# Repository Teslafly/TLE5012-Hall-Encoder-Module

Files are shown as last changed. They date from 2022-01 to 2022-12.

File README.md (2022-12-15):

# TLE5012-Hall-Encoder-Module
Breakout/mounting board for the TLE5012 hall encoder to use with the vesc motor controller project.

(Pictures are from my nearly identical as5047 encoder board at https://github.com/Teslafly/AS5047-Hall-Encoder-Module)

encoder boards with both connector orentations
top and bottom
example cables
kitting hardware
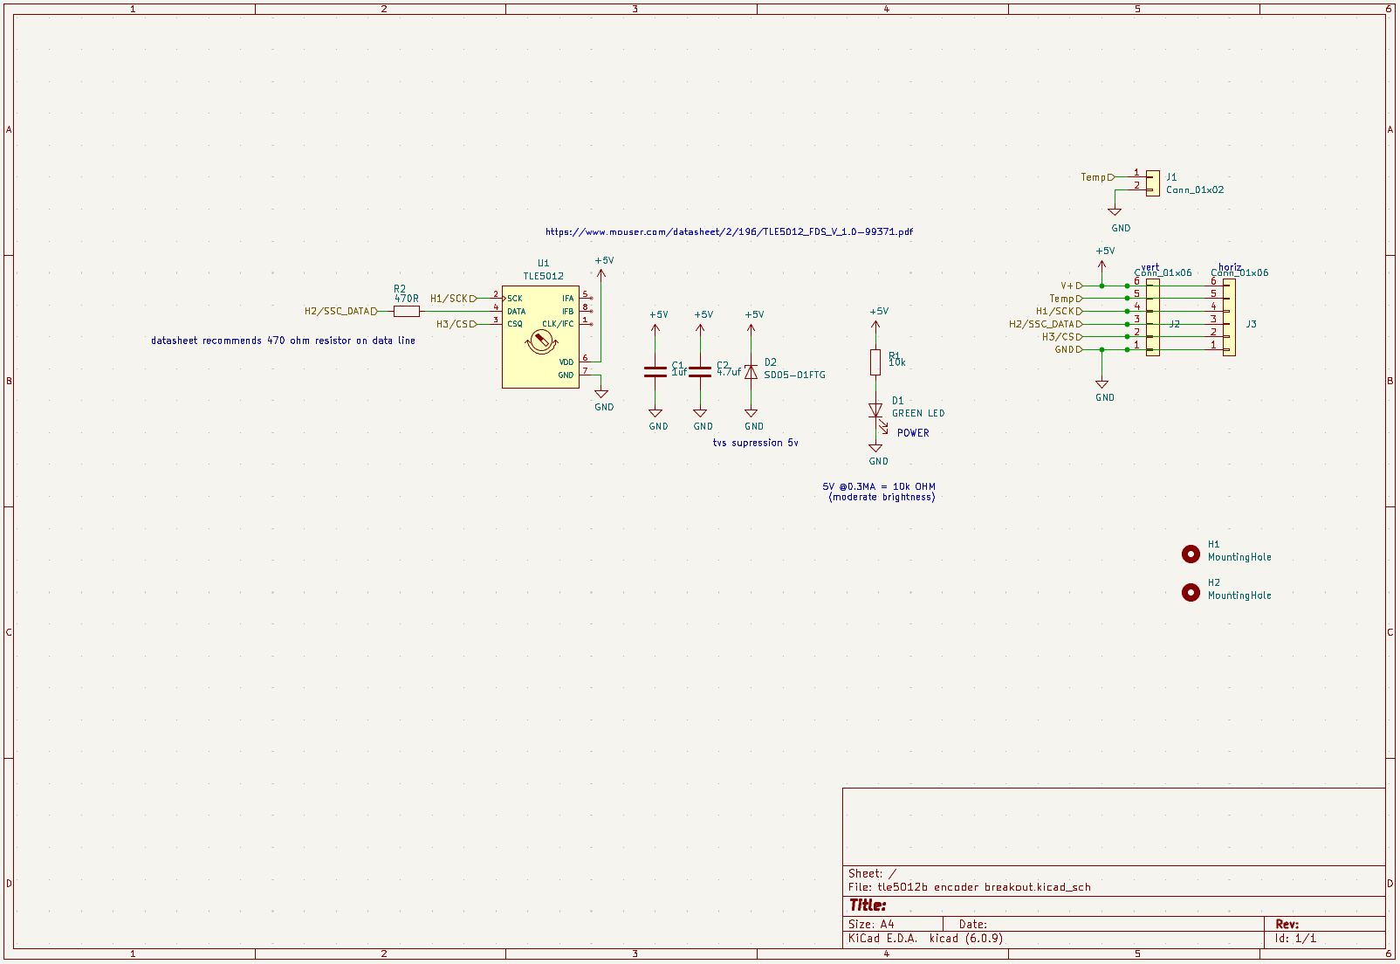
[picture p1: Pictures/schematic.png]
schematic


# Mounting:
- The mounting holes fit an m3 screw and are 16mm apart center to center.
- If the pcb cannot recess into the motor, a 3d printed shim (file link) can raise the encoder and provide clearance. If the motor gets too hot, the shim may be laser cut or milled out of a more resistant material.
- This encoder works with a diametric magnet fixed to the motor shaft. 
    - The magnet must be centered on the shaft. The encoder must be centered over the center of the magnet.
    - I find good results with a 6x2mm or 6x3mm neodymium magnet placed 1-5mm away from the face of the encoder.
    - Magnet example: https://www.aliexpress.us/item/3256801356246959.html

# Building:
- This pcb can be hand soldered easially.
- You can use either horizontal or vertical jst gh connectors for each connector placement. The vertical data connector should be placed with pins outwards to maintain the same pinout between the horizontal/vertical data connector options.
- As the temperature sensor connector is unpolarised, either horizontal or vertical connector can be placed on the same footprint. see pictures.

# JST GH mating connectors and making cables:
- If you do not have a crimper for JST GH crimps, they are fiddley and are hard to crimp properly.
I recommend either getting a male to male JST GH cable and cutting it to splice into a longer encoder cable, or doing the same with a precrimped silicone wire kit like this:
  - https://www.amazon.com/Pre-Crimped-Connectors-Pixhawk2-Pixracer-Silicone/dp/B07PBHN7TM/
  - Silicone wire is preferred due to it's durability and heat resistance. If you use pvc wire you should reinforce around the male GH connector with silocone rtv.

- The jst gh data connector has the same pinout as the JST PH vesc hall sensor connector.
however, note that some vesc hardwares that have swapped to JST GH connectors have reversed pinouts.
aka the cable must connect pins 1<->6, 2<->5, etc so that the locking clips are reversed from each other.
  - THIS IS NOT THE CASE ON ALL HARDWARES. CHECK YOUR PINOUT BEFORE POWERING.
    A REVERSED PINOUT WILL DESTROY THE ENCODER AS 5V AND GND ARE SWAPPED.
  - (The sensor should get lukewarm during operation. If it gets really hot then it's dead or a wire is shorted)

- Also, your vesc hardware must not have filters placed on the hall port pins. 
these filters must be removed for this encoder to work if present. They are present on all vesc hw 4.2, and nearly all flipsky boards. Trampa hw 6.0+ do not have these filters and will work as is.

### Wire:
I recommend using sheilded wire. usb cable will work in a pinch if you omot the temp wire and use the sheild for gnd. but ~28awg 6 core sheilded cable is ideal. the sheild should be connected to the gnd pin on the vesc side, and unconnected on the sensor side. you must keep all wires close to each other to get good signal integrity when splicing /crimping the end connectors.
If you cannot source sheilded wire, you will get acceptable results by keeping the wires close, and routing the cable away from the phase wires of the motor.
It is recommended that the data cable is kept under 0.5 meters. If that is not possible then sheilded wire must be used and attention to detail excercised in cable construction.

# Testing:
- This sensor runs best at 5V input power. 3.3V operation is not gaurenteed but will not cause damage.
- The led on the pcb should glow somewhat dimly. It is not blindingly bright.
- The sensor IC should get lukewarm during operation. If it gets really hot then it's dead or a wire is shorted

- You can troubleshoot/test the signal integrity of your cable and encoder functionality with the "`encoder`" command in the vesc terminal. 
  - The error rate should be very close to zero.
  - If it is above 0.5% then you should troubleshoot your setup and improve signal integrity. 
  - 99+% generally means that all communication with the encoder has failed. The wiring may be wrong, the sensor dead, or your vesc has hall port filters that need to be removed and shorted.
- when viewing the encoder angle in the vest-tool realtime view, the encoder value should change smoothly through the entire 360 degrees. If it is jumpy you probably have a signal integrity issue
- If the sensor cable is poorly routed/sheilded, high motor currents can cause noise that increases the encoder error rate. If you experience encoder faults during acceleration, check for intermittent opens in all signals and try rerouting the sensor cable away from motor phase wires and battery cables.
- a 3d printable test jig using a 608 bearing and 6mm magnet is included in the "`608 bearing test holder`" folder.

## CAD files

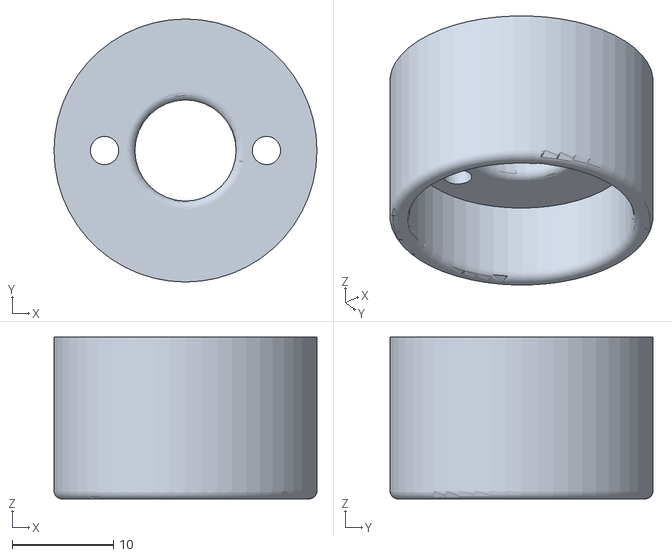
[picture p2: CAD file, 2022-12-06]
608 bearing test holder/bearing base-PartBody.stl
26.0 x 26.0 x 16.0

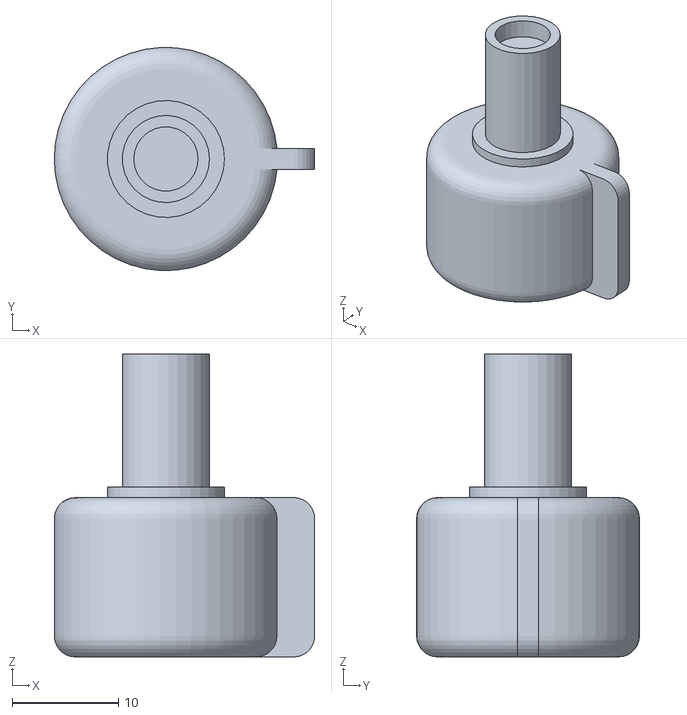
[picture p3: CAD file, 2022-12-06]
608 bearing test holder/knob-Body.stl
24.5 x 21.0 x 28.5

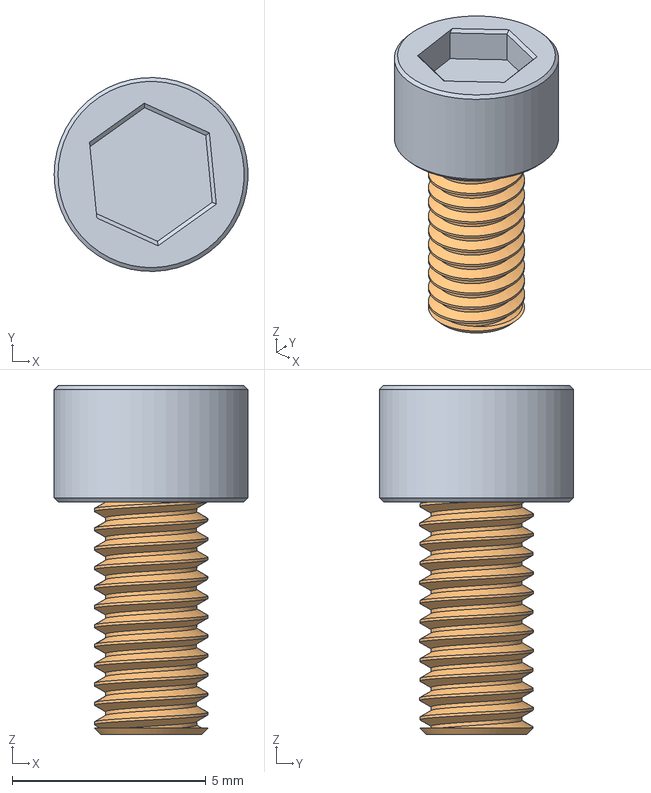
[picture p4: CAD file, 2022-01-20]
3d models/screw M3 6mm .step
5.00 x 5.00 x 9.00 mm

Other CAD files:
608 bearing test holder/knob.FCStd
608 bearing test holder/bearing base.FCStd

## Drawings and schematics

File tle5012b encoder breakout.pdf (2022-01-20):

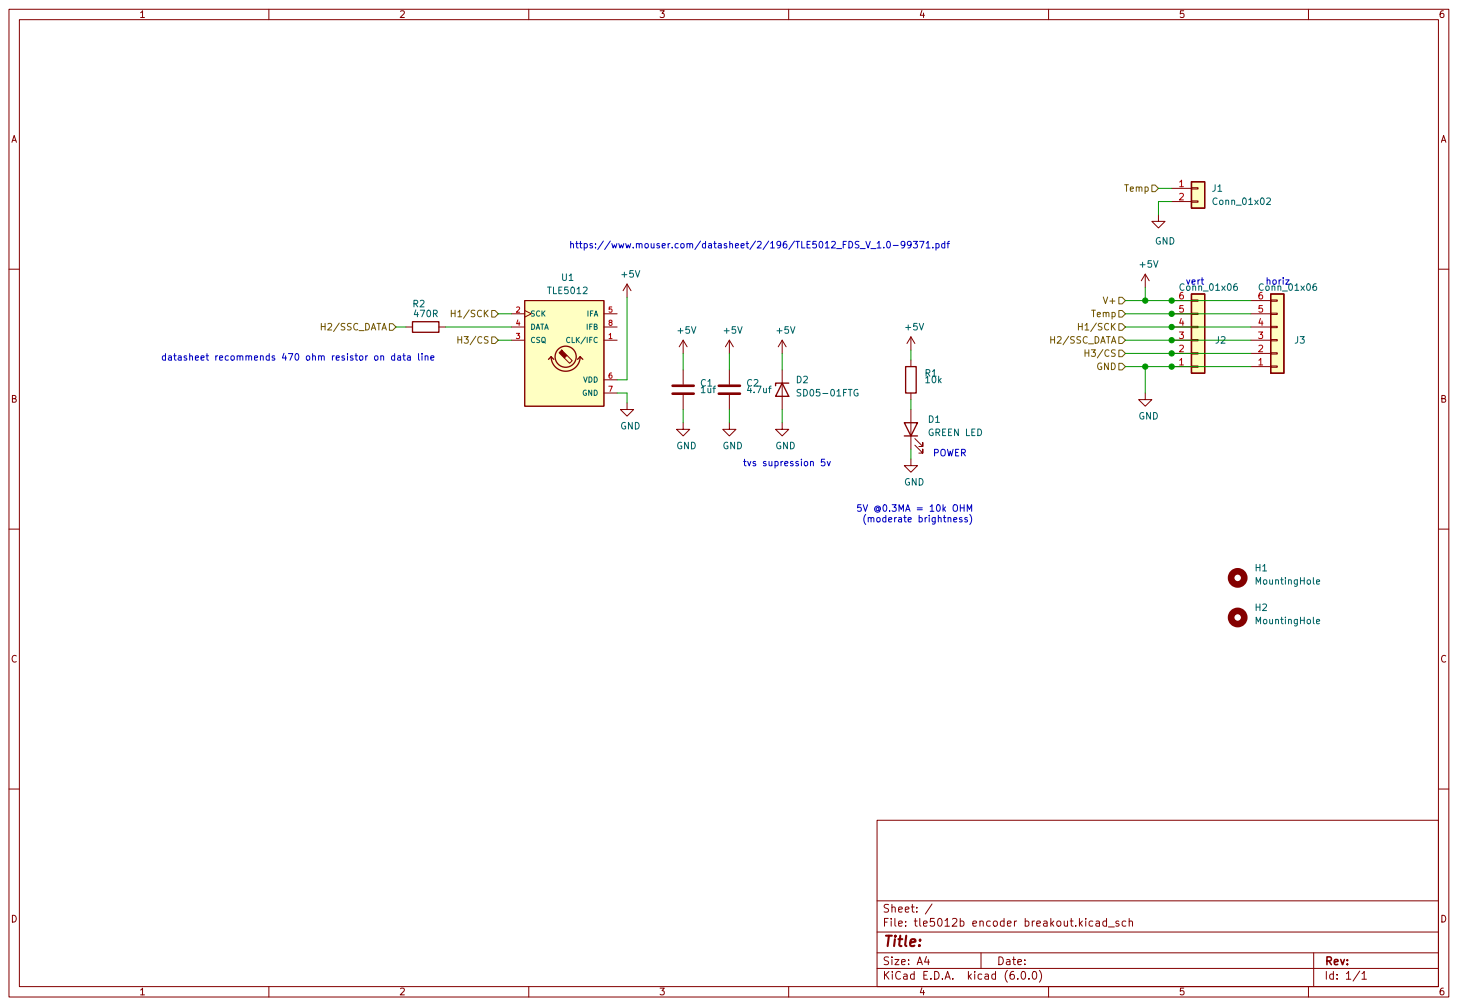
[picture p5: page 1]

https://www.mouser.com/datasheet/2/196/TLE5012_FDS_V_1.0-99371.pdfPOWER

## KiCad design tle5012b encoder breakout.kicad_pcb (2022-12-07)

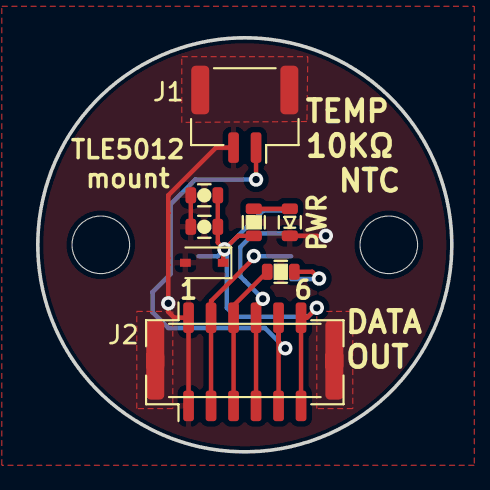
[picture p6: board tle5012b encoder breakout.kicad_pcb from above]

Board: 2 copper layers, 23.0 x 23.0 mm, 12 parts (1 on the bottom side), 8 nets.

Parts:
C1: 1uf; C_0603
C2: 4.7uf; C_0603
D1: GREEN LED; D_0603
D2: SD05-01FTG; D_SOD-323
H1, H2: MountingHole; MountingHole_3.2mm_M3
J1: Conn_01x02; JST_GH_SM02B-GHS-TB_1x02-1MP_P1.25mm_Horizontal
J2: data-V; JST_GH_BM06B-GHS-TBT_1x06-1MP_P1.25mm_Vertical
J3: data-H; JST_GH_SM06B-GHS-TB_1x06-1MP_P1.25mm_Horizontal
R1: 10k; R_0603
R2: 470R; R_0603
U1: TLE5012; SO-8_3.9x4.9mm_P1.27mm

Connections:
+5V: C1.1, C2.1, D2.1 (K), J2.6, J3.6, R1.1, U1.6 (VDD)
/H1/SCK: J2.4, J3.4, U1.2 (SCK)
/H2/SSC_DATA: J2.3, J3.3, R2.1
/H3/CS: J2.2, J3.2, U1.3 (CSQ)
/Temp: J1.1, J2.5, J3.5
GND: C1.2, C2.2, D1.C (K), D2.2 (A), J1.2, J1.MP, J2.1, J2.MP, J3.1, J3.MP, U1.7 (GND)
unnamed: D1.A, R1.2
unnamed: R2.2, U1.4 (DATA)

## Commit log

2022-01-20 Initial commit of v1
    [screw M3 6mm .step, tle5012b encoder breakout.kicad_pcb, tle5012b encoder breakout.kicad_sch]
2022-12-06 add 3d printed test jig files
    [bearing base-PartBody.stl, bearing base.FCStd, knob-Body.stl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]
2022-12-07 update kicad version
    [tle5012b encoder breakout.kicad_sch]
2022-12-07 update schematic picture
2022-12-07 Connected connector mounting pads to gnd plane for structural support
    [tle5012b encoder breakout.kicad_pcb, tle5012b encoder breakout.kicad_sch]
2022-12-15 Update README.md
    add link to other board
